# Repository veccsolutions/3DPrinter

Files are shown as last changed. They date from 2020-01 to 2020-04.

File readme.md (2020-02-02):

My HyperCube - soon to be named a super cube.

# Summary
The original HyperCube design was a good choice for my first printer. I had my brother print off the parts I needed. I ended up melting one and had my co-worker re-print it.

I didn't use the cheap electronic parts that were in the original built, instead I went all in and got some pretty nice stuff:
* <a href="https://e3d-online.com/v6-all-metal-hotend">E3D V6 hotend</a>
* <a href="https://e3d-online.com/titan-extruder">E3D Titan Extruder</a> with Compact but Powerful Motor
* <a href="https://shop.prusa3d.com/en/mk3mk3s/214-powder-coated-spring-steel-sheet.html">Prusa Spring Steel Sheet</a>
* <a href="https://www.amazon.com/dp/B07JLQW3XW">Anet A8 12-volt heat bed</a>
* <a href="https://www.amazon.com/dp/B007K2H0GI">MeanWell NES-350-12</a> volt power supply
* <a href="https://ultimachine.com/products/archim2">Archim2 controller</a>
* 2 <a href="https://ultimachine.com/products/kysan-1124090-nema-17-stepper-motor">Kysan 1124090 Nema stepper motors</a> (X/Y axis)
* <a href="https://www.amazon.com/dp/B07RRY5MYZ/">Switch/Plug combo</a>

Building it was fun. Just make sure to get the t-nuts that for the aluminum that don't require you to slide them in from the end. Lesson learned...the hard way.

Getting it to actually print was a challenge. A big challenge. Most of it had to do with the firmware. Because it's a custom printer you'll need custom firmware. Because it's the Archim2 board with a 32-bit CPU it meant using the Marlin 2.0 branch.

The example config for Archim2 did not compile because the config was wrong for the SPI and a few other things. It took about an hour or 2 to get it to actually compile and boot up on the Archim correctly. It then took another week of tinkering with it and figuring out steps per MM, correct orientation of wires, end stop modes, homing types, etc to get to it finally work correctly.

Once I got the head moving in the right directions, and the correct amounts, I ran into a weird problem. If I moved the head slowly it was accurate. Very accurate (to 1/100th of a millimeter). If it moved the head quickly, it would jump all over the place. That took a long time to figure out. It was the acceleration. Once I capped it at 500 it worked flawlessly. It prints a bit slower than I would like, but its printing perfectly. It's a work in progress.

After all of that, I got to a point where I could customize it to make it my own and better than ever.

The most annoying issue I ran into with printing on the HyperCube is the Z-Axis. There's not enough meat to the carriages that holds it up on the rods to reliably hold the gantry stable. It kept sagging after one or 2 prints. Because of that, it's the first thing I fixed. I replaced the brackets with something far more substantial and it now holds it perfectly.

After the Z-Axis fix, I print pretty well almost every time. Maybe 1 in 7 have a problem, like me forgetting to wipe off the build plate....

Now I can print, it's time to mount the electronics and make this thing safe to keep plugged in. Because right now everything is just spilled out on the table. The power cord is screwed right into the power supply with no support. And electronics are open and waiting to have screws dropped on them.

I then decided to try mounting my electronics on the back. That didn't go very far. I built a mount for the Raspberry, it's a simple thin flat piece of plastic with holes and some standoffs to hold the Pi. It worked. But I didn't like having it on the back so I didn't go much further on mounting things to the back.

I then started hunting around and came across something someone built on Thingiverse. They built a bottom storage area for the HyperCube Evolution. It wouldn't work for the original HyperCube due to size differences, but it was a starting point. Now, I'm building a base for the HyperCube using modular plates to attach whatever, wherever underneat the HyperCube.

On a side note, it enrages me that nobody posts the real source of the STL files. STL files are NOT source. Sure you could change them. But it's akin to opening a hex editor and modifying a binary file. So, I'm sharing my SCAD files under the MIT license, like I do with everything else I put out there for people to use.

# Things I changed
## Z Axis (the part that goes up and down)
The first thing I really didn't like was the Z axis and the way it was mounted. It was extremely unstable and wouldn't stay level because of it. I was also unable to keep it square/level on both sides.

 Even after moving the sliding rods to the sides (which helped a lot), the mounts were just to small. So I rebuilt those.
 
 They are longer and a bit more beefy. They now go underneath the arms to prevent them from sagging. This added a huge amount of stability and so far the only time I have to level the bed is when I push down really hard or change something on the bed platform itself.

 ## Extruder (the part the pushes the filament)
 The second thing was the extruder, I wanted something nicer so I ended up getting an E3D Titan extruder and building a mount for it.

 The differences in prints between using a simple extruder and something with a .9&deg; step and a 3:1 reducing gear was insane. I can't believe how much better the prints are coming out.

# Things I've added
## Rear Electronics Mounts (not used anymore)
| Part | File |
|-|-|
| Raspberry Pi | <a href="Electronics Bay\Rear Mounted\PiMount\Pi Mount.scad">Electronics Bay\Rear Mounted\PiMount\Pi Mount.scad |

## Bottom electronics bay
An area underneath the printer to mount the electronics (plates) and a drawer to hold tools and other non-sense (coming soon)
<a href="Electronics Bay/Bottom Mounted">Electronics Bay/Bottom Mounted</a>

* Corner brackets to sit the printer on and mount plates to <a href="Electronics Bay/Bottom Mounted/Corner Stand.scad">Corner Stand.scad</a>
* A plate to hold the Raspberry Pi <a href="Electronics Bay/Bottom Mounted/PI Mount Combined.scad">PI Mount Combined.scad</a>
* A plate to put a switch and plug in to <a href="Electronics Bay/Bottom Mounted/Switch Plate.scad">Switch Plate.scad</a>
* Plates for the NES-350-12 power supply (coming soon)
* A plate for the Archim2 controller board (coming soon)

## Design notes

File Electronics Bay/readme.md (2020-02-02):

Choose either bottom mount or rear mount.

The bottom mount will lift your printer up about 65mm.

The bottom mount option contains brackets for a Raspberry PI 4, MeanWell NES-350-12 power supply, an Archim2 controller board and a switch/plug for a cord.

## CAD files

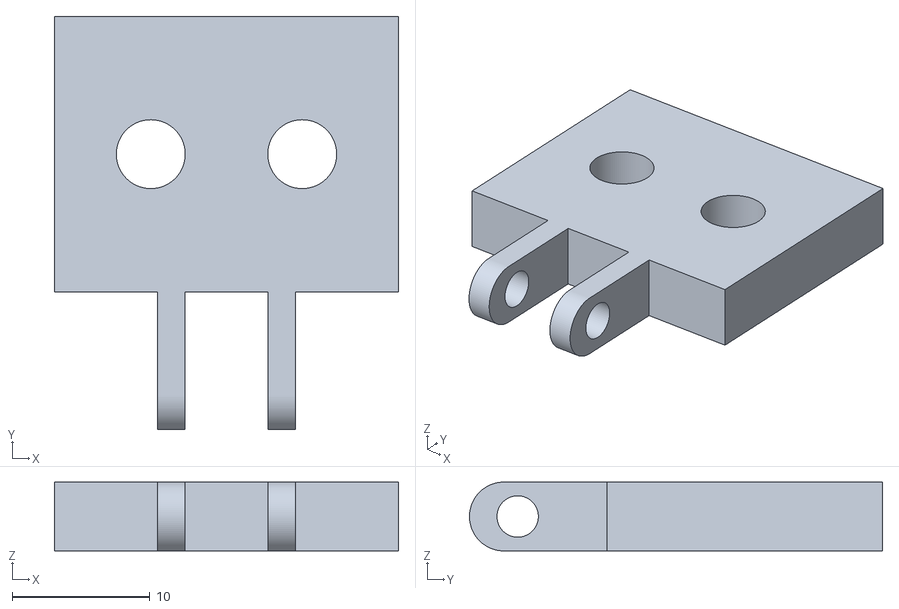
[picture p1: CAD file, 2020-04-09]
Camera Mount/Frame Mount.stl
25.0 x 30.0 x 5.00

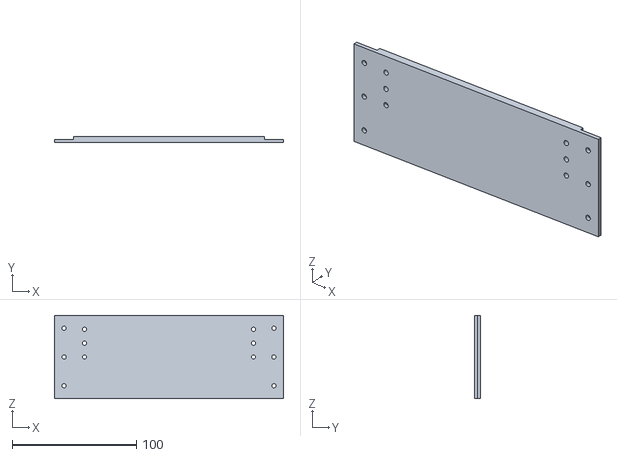
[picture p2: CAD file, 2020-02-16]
Electronics Bay/Bottom Mounted/PI Mount Panel.stl
184.5 x 5.15 x 67.0

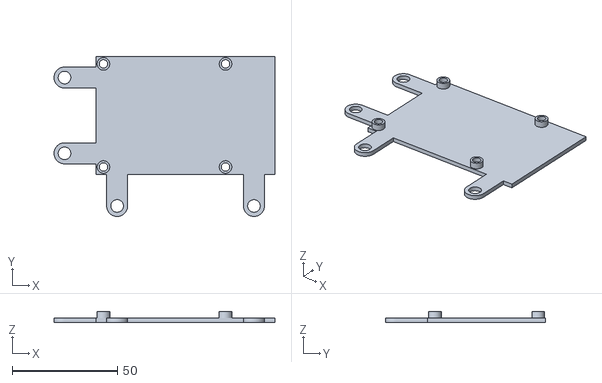
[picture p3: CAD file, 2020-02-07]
Electronics Bay/Rear Mounted/PiMount/Pi Mount.stl
105.0 x 76.0 x 5.00

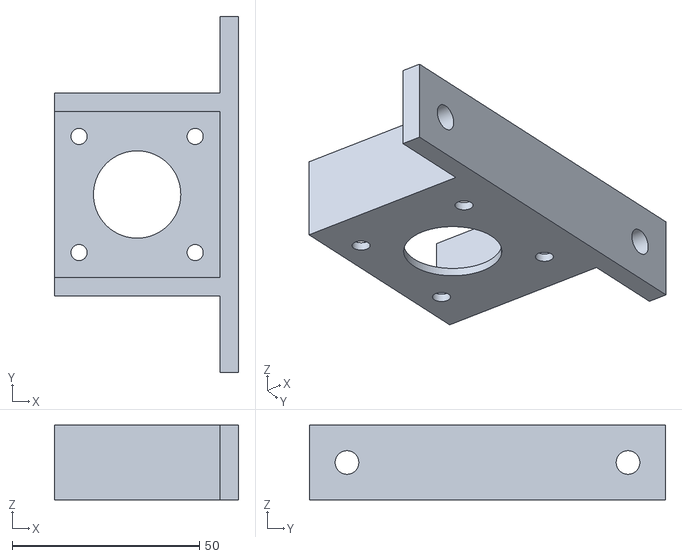
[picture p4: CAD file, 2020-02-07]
Extruder Bracket/Bracket.stl
49.2 x 95.0 x 20.0

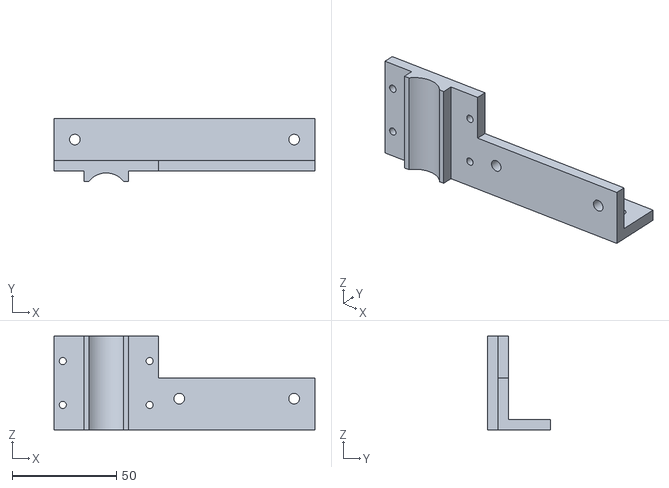
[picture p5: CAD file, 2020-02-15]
Z-Gantry/Right Rail.stl
125.0 x 30.0 x 45.0

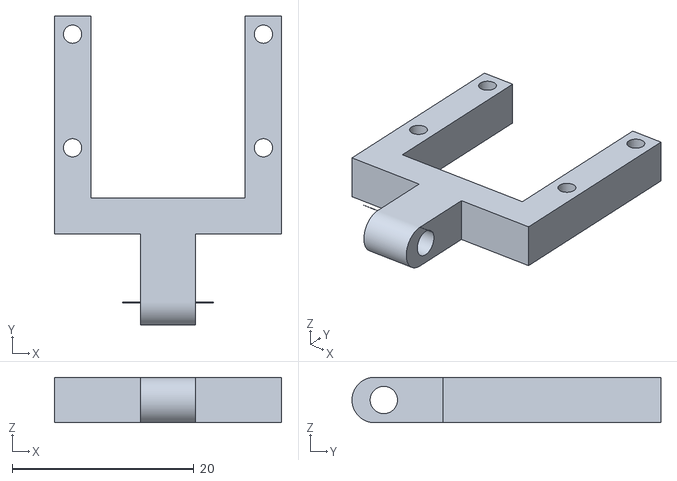
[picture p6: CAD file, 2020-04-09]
Camera Mount/Camera Mount.stl
25.0 x 34.0 x 5.00

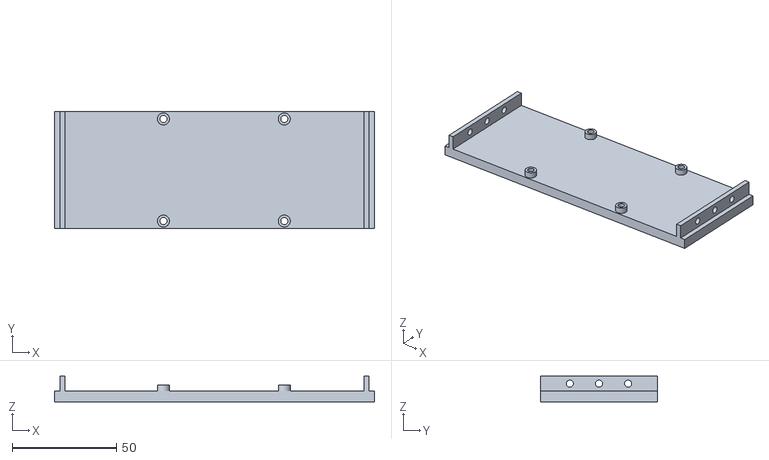
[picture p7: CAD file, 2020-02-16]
Electronics Bay/Bottom Mounted/PI Mount Bottom.stl
153.6 x 56.0 x 12.3

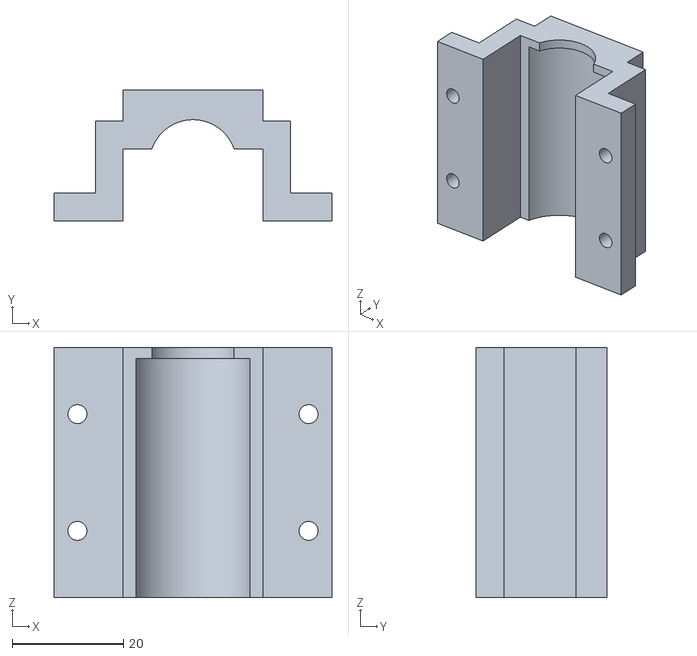
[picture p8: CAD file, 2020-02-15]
Z-Gantry/Bearing Clamp.stl
50.0 x 23.6 x 45.0

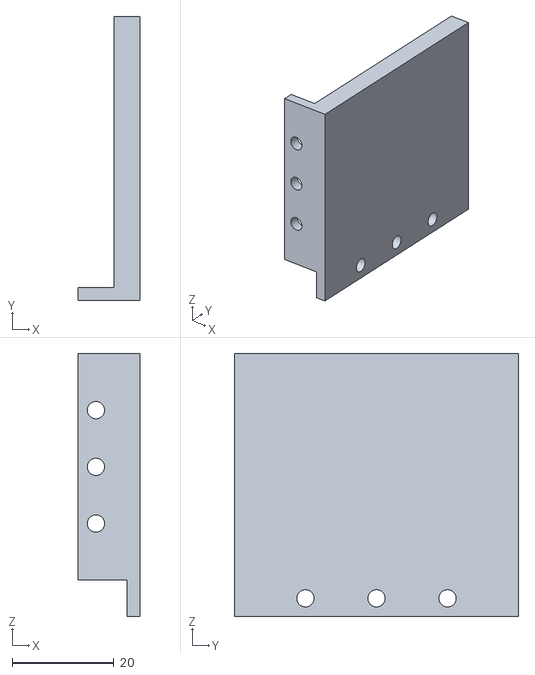
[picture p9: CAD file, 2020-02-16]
Electronics Bay/Bottom Mounted/PI Mount Left Brace.stl
12.3 x 56.0 x 51.8

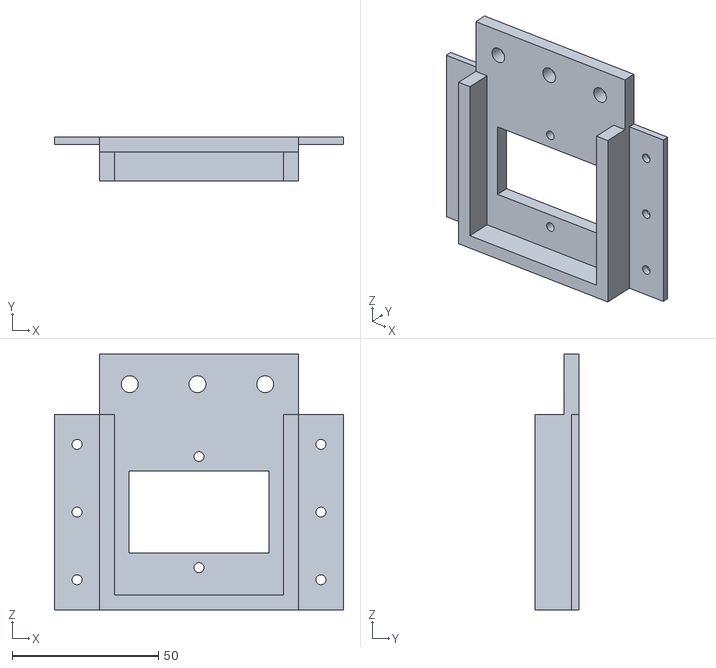
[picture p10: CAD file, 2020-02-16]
Electronics Bay/Bottom Mounted/Switch Plate.stl
98.9 x 15.2 x 87.5

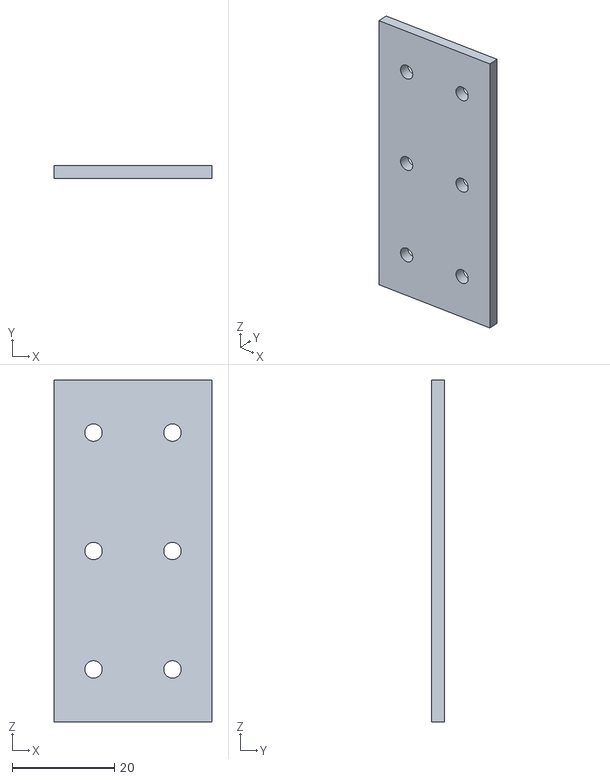
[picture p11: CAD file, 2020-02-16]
Electronics Bay/Bottom Mounted/Plate Joint.stl
30.9 x 2.58 x 67.0

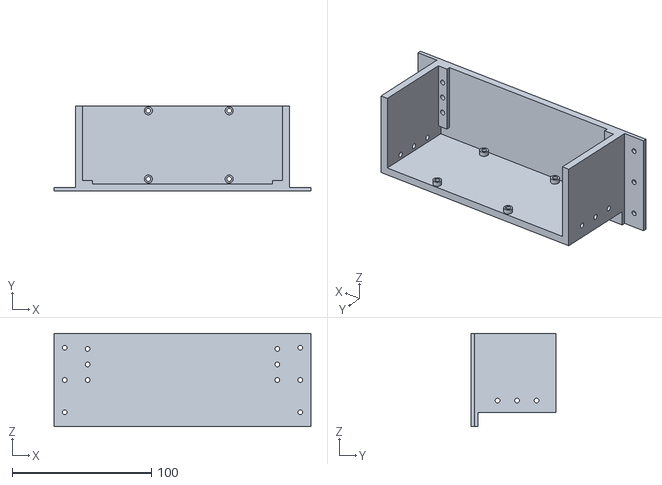
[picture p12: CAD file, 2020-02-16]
Electronics Bay/Bottom Mounted/PI Mount Combined.stl
184.5 x 61.1 x 67.0

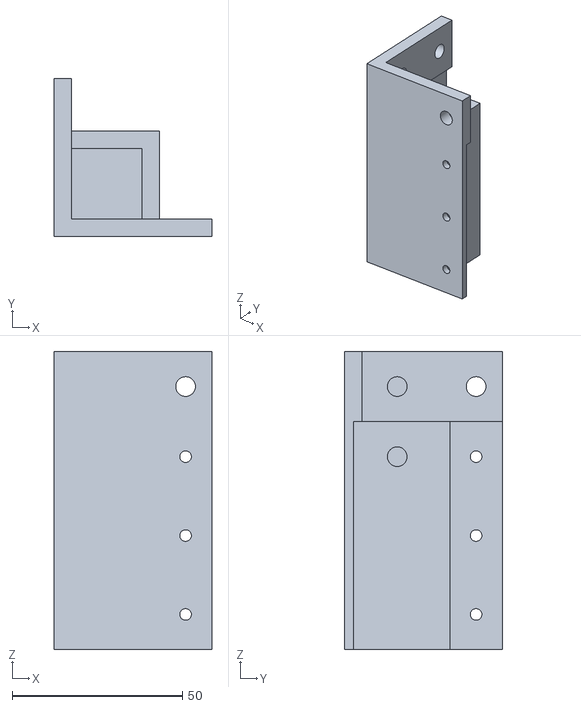
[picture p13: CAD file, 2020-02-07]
Electronics Bay/Bottom Mounted/Corner Stand.stl
46.4 x 46.4 x 87.5

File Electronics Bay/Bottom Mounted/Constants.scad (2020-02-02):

petgShrinkage = 1.03;

shrinkage = petgShrinkage; //done so we can do pla if desired
standHeight = 65 * shrinkage;
aluminumHeight = 20 * shrinkage;
aluminumWidth = 20 * shrinkage;
standHoleCount = 3;
standLargeScrewOffset = 10 * shrinkage;
standThickness = 5 * shrinkage;
standFlangeWidth = 15 * shrinkage;
standFlangeHoleOffset = 10 * shrinkage;
topRailHoleOffset = 10 * shrinkage;

standFlangeThickness = standThickness / 2;
standFlangeHoleLength = (standHeight - (standFlangeHoleOffset * 2));
standFlangeHoleStep = (standHeight - (standFlangeHoleOffset * 2)) / (standHoleCount - 1);

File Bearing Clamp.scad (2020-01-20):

thickness = 5;
bearingHeight = 50;
bearingDiameter = 21;
bearingCarriageLength=50;
bearingCarriageHeight = bearingHeight;
footWidth = (bearingCarriageLength - bearingDiameter) / 2 - 1;
clampHeight = bearingDiameter - thickness - 1;

module cylinder_outer(height,radius,fn)
{
   fudge = 1/cos(180/fn);
   cylinder(h=height,r=radius*fudge,$fn=fn);
}

module threeMMScrew()
{
    cylinder_outer(thickness+.1, 3.2/2, 100);
}

module carriageHoles()
{
    translate([0, bearingCarriageHeight / 4, 0]) {
        threeMMScrew();
    }
    translate([0, bearingCarriageHeight / 4 * 2, 0]) {
        threeMMScrew();
    }
    translate([0, bearingCarriageHeight / 4 * 3, 0]) {
        threeMMScrew();
    }
}

module feet()
{
    
    color([1,0,0])
    translate ([0, 0, 0])
    {
        difference()
        {
            cube([footWidth, bearingHeight, thickness]);
            translate([thickness,0,0]){
                carriageHoles();
            }
        }
    }
    
    color([1,0,0])
    translate([footWidth + bearingDiameter + 2, 0, 0])
    {
        difference()
        {
            cube([footWidth, bearingHeight, thickness]);
            translate([footWidth - thickness,0,0]){
                carriageHoles();
            }
        }
    }
}

module sidewalls()
{
    color([0,1,0])
    translate([footWidth - thickness, 0, thickness])
    {
        cube([thickness, bearingHeight, clampHeight]);
    }
    color([0,1,0])
        translate([footWidth + bearingDiameter + 2, 0, thickness])
    {
        cube([thickness, bearingHeight, clampHeight]);
    }
}

module bearingClamp()
{
    color([.5,1,1])
    translate([footWidth, 0, thickness*2-1])
    {
        difference()
        {
            cube([bearingDiameter+2, bearingHeight, bearingDiameter / 2 + 3]);
            translate([bearingDiameter / 2 + 1, 0, 0])
            {
                rotate([-90,0,0])
                {
                    cylinder_outer(bearingHeight, bearingDiameter / 2, 100);
                }
            }
        }
    }
}


feet();
sidewalls();
bearingClamp();

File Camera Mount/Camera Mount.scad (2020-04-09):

include <Common.scad>;

CameraMount();

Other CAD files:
Z-Gantry/Left Rail.stl
Electronics Bay/Bottom Mounted/PI Mount Right Brace.stl
Camera Mount/Combined.scad
Camera Mount/Common.scad
Camera Mount/Frame Mount.scad
Electronics Bay/Bottom Mounted/Common.scad
Electronics Bay/Bottom Mounted/Corner Stand.scad
Electronics Bay/Bottom Mounted/PI Mount Bottom.scad
Electronics Bay/Bottom Mounted/PI Mount Combined.scad
Electronics Bay/Bottom Mounted/PI Mount Left Brace.scad
Electronics Bay/Bottom Mounted/PI Mount Panel.scad
Electronics Bay/Bottom Mounted/PI Mount Right Brace.scad
Electronics Bay/Bottom Mounted/PI Mount.scad
Electronics Bay/Bottom Mounted/Plate Joint.scad
Electronics Bay/Bottom Mounted/Switch Plate.scad
Electronics Bay/Rear Mounted/PiMount/Pi Mount.scad
Electronics Bay/Rear Mounted/Power Supply/MeanWell NES-350-12.scad
Extruder Bracket/Bracket.scad
Z-Gantry/Bearing Clamp.scad
Z-Gantry/Combined Rail.scad
Z-Gantry/Common.scad
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

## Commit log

2020-01-20 Initial attempt at a new set of bearing clamps
    [Bearing Carriage.scad, Bearing Clamp.scad, Left Rail.scad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]
2020-01-20 Shortened the bearing holder on the carriage
    [Bearing Carriage.scad]
2020-01-22 Moved the files
    [Bearing Carriage.scad, Bearing Clamp.scad, Left Rail.scad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]
2020-01-25 Using a new style
    [Bracket.scad]
2020-01-25 Replaced the bracket with a modified one that I found online
    [Bracket.scad]
2020-01-26 Starting on the power supply bracket
    [MeanWell NES-350-12.scad]
2020-01-28 Added the pi mount
    [Pi Mount.scad]
2020-02-01 Starting powersupply mount
    [MeanWell NES-350-12.scad]
2020-02-01 Working on the bottom electronics bay
    [Common.scad, Constants.scad, Corner Stand.scad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]
2020-02-02 Added the PI Mount pieces (needs to be reduced)
    [Common.scad, Constants.scad, Corner Stand.scad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]
2020-02-02 Moved rear mount stuff to the correct folder
    [MeanWell NES-350-12.scad, Pi Mount.scad]
2020-02-07 Added stl files for github viewers
    [Bearing Carriage.stl, Bearing Clamp.stl, Bracket.stl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]
2020-02-15 Re designed the z gantry rails and clamps - crazy stable now
    [Bearing Carriage.scad, Bearing Clamp.scad, Bearing Clamp.stl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]
2020-02-15 Removed the superfluous bearing carriage
    [Bearing Carriage.scad, Bearing Carriage.stl]
2020-02-16 Refreshed the plates after some updates
    [PI Mount Bottom.stl, PI Mount Combined.stl, PI Mount Left Brace.stl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]
2020-04-09 Added the camera mount
    [Camera Mount.scad, Camera Mount.stl, Combined.scad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]
